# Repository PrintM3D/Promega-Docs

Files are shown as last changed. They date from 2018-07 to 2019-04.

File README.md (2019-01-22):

# Welcome!

Welcome to the  M3D Promega's User Manual.

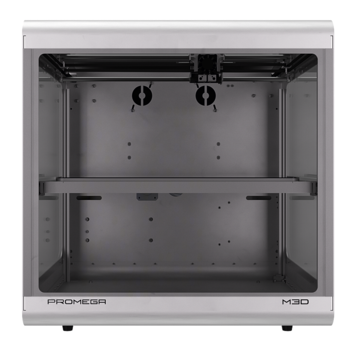
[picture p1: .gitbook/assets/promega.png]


## Features

### Expandable

The Promega is expandable, meaning you can customize it to suit your needs. These are 4 possible extruder configurations.

{% tabs %}
{% tab title="Compound Printing" %}
The Compound nozzle is a dual mixing nozzle, which takes in two filaments and either prints one at a time or mixes them together. 

A standard Promega will come with this extruder.

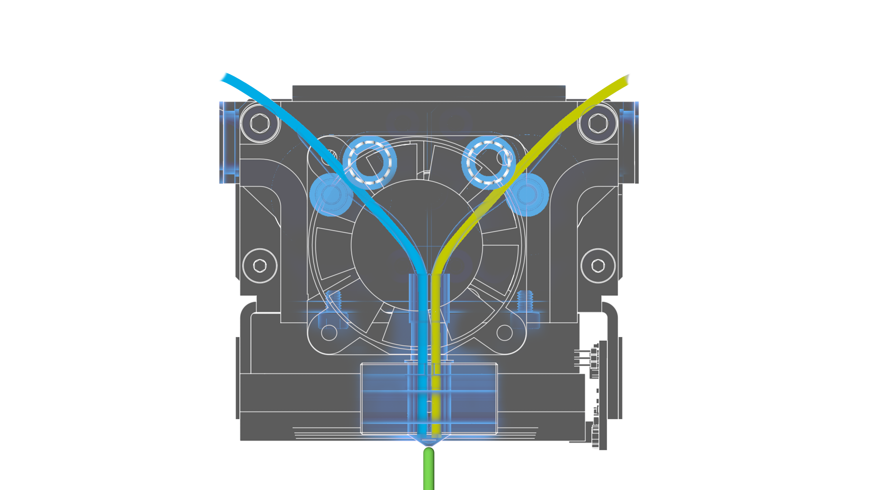
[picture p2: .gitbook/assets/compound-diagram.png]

{% endtab %}

{% tab title="Dual Printing" %}
  
The K'Tana hot end is two, independent nozzles for dual printing. 

K'Tana nozzles are seamless, long nozzles that include a thin-wall heat break to reduce energy consumption and eliminate leaks.

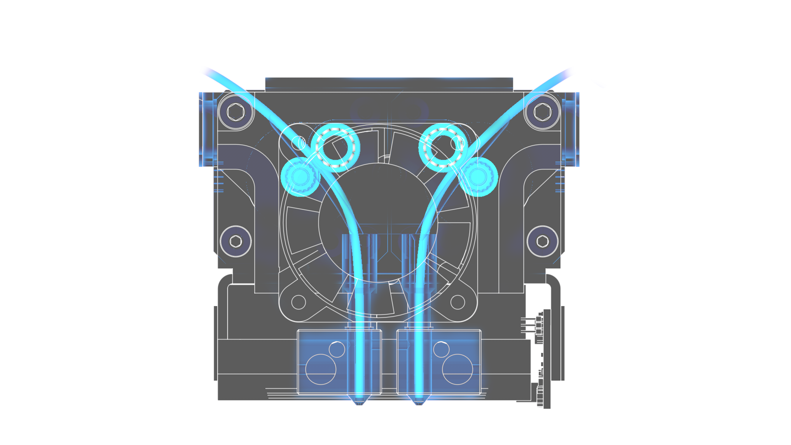
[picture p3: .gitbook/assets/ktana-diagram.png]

{% endtab %}

{% tab title="Quad Printing" %}
  
The Quad extruder takes in four filaments and can either print one at a time or mix for blended colors.

You can create beautiful color prints using our CMYK color-calibrated mixing filament.

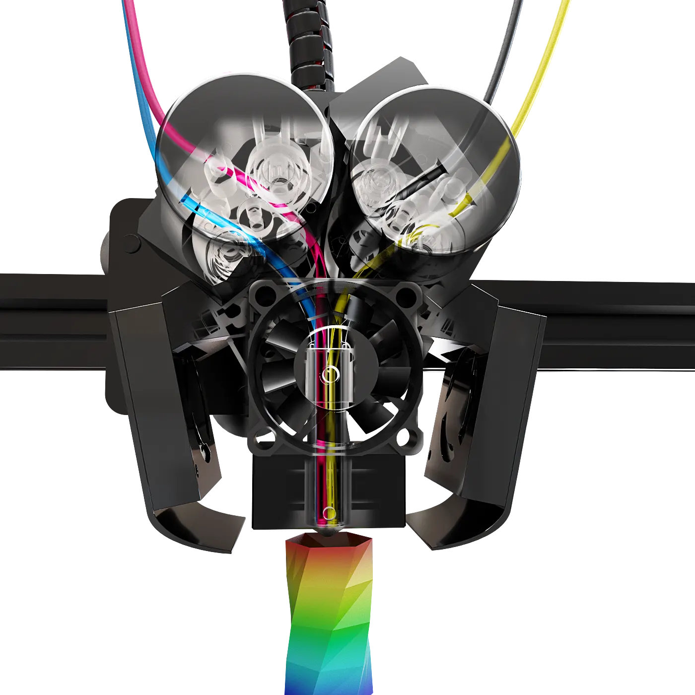
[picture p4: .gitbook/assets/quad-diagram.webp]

{% endtab %}

{% tab title="High Temp Printing" %}
Our high-temp extruder add-on allows you to extrude materials up to 350 C. 

This upgrade is ideal for printing high-temp materials such as PEEK, if you are producing small prints. 

For larger prints, you may need a more robust system upgrade. If you are interested in this, please fill out this [form](https://airtable.com/shrPYVe4EY4mXUM4e).
{% endtab %}
{% endtabs %}

Feel free to browse the [part store](https://store.printm3d.com/collections/parts) for more.

### 20" All Metal Frame

Fully enclosed in a 20" all-metal frame.

### 15.3" Cubic Build Volume

15.3"-cubed build volume makes printing just about anything possible.

### Open Source

Both the [Duet3D electronics](https://www.duet3d.com/) and the [Promega parts](documentation/) are open-sourced.

## Where To Start

Please start with the [Beginner Guides](beginners-setup-guides/).

If the Beginner Guides aren't enough, try our [Advanced Guides](advanced-setup-guides/). 

## **Other Resources**

### Duet3D Board

#### [Firmware/Software](https://github.com/PrintM3D?tab=repositories)

#### [Duet Maestro](https://duet3d.dozuki.com/c/Duet_2_Maestro)

#### [Duet GCodes](https://duet3d.dozuki.com/Wiki/GCode)

### Promega Parts Store

#### [Linked Here!](https://store.printm3d.com/collections/parts/printer-model_m3d-promega)

### Open Source 

#### [Public Google Drive](https://drive.google.com/open?id=1cmnAcQU7NjgBqAub60Pz7tJyY-e5qH1w)

{% hint style="info" %}
Houses all iterations of:

* SD Cards
* Slicer
* Printed Part. 
{% endhint %}

### **Q&A Promega Users**

[Submit Issue](https://github.com/PrintM3D/Promega/issues). Allows you to search for existing issues to upvote them. 

Submit a new issue if you do not find one.

### Contributing

Please feel free to add suggestions to any of the guides by creating a pull-request or issue on [GitHub](https://github.com/PrintM3D/Promega-Docs/issues). This manual is hosted in Github.com via Gitbook.com.

The main way to collaborate to the guides is to become a collaborator. But sometimes you simply want to submit a small contribution, without becoming a regular collaborator.

On GitHub, one can use the popular _Pull Request_ feature. To do so, you would clone [https://github.com/PrintM3D/Promega-Docs](https://github.com/PrintM3D/Promega-Docs), make changes on your own copy, and submit back your changes by submitting a _Pull Request_ to M3D. Then we will review the changes accordingly.

#### Let's Get Started!

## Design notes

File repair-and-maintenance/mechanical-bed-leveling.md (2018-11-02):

# Mechanical Bed Leveling

### Leveling the Bed

As covered in the [Bed Leveling & Probing](../advanced-setup-guides/bed-leveling-and-probing.md) guide, bed leveling compensation will work for differences of about 3mm across the entire bed. Leveling your bed can be done by skipping teeth on the bed in specific corners. If your bed is extremely un-leveled, it will not be movable by hand.

Look at your bed and determine if one side is visibly higher than the other side.

Remove the binder clip if you have placed one on the Z-motor belt.

Gently pull up on the corner that you want to skip. Apply pressure until you feel the corner give with a loud click. 

{% hint style="warning" %}
Do not skip the bed near the belt clamps as it can break your belt clamps.
{% endhint %}

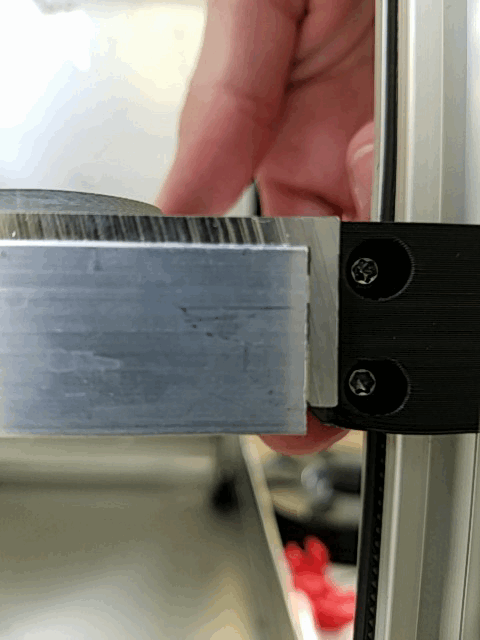
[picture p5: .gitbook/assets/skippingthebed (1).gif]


Once the bed is level enough to the point where it drops by itself, move the bed up to the nozzle by hand. The bed is best lifted up from the points pictured below. 

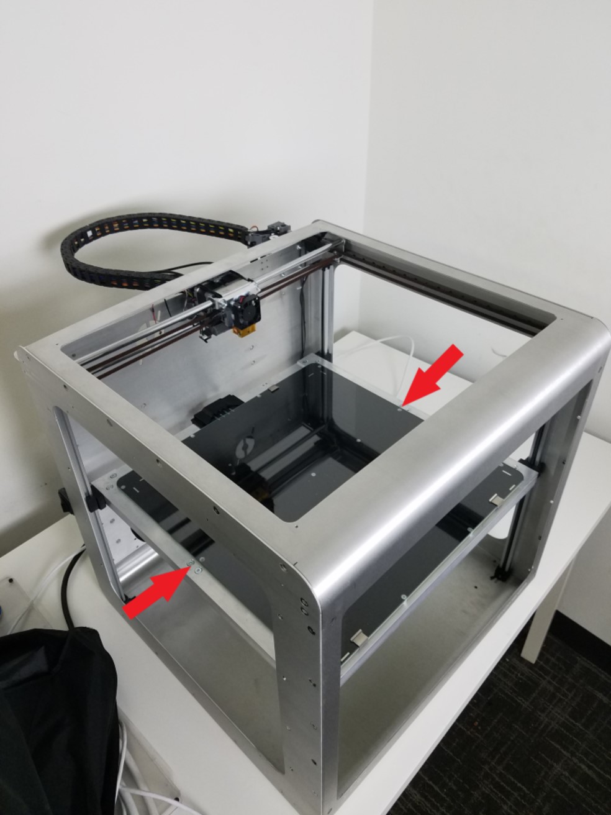
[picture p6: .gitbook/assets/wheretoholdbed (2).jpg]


Lift slowly or you will skip the bed. 

{% hint style="warning" %}
Moving the bed too fast can also fry your Duet board, so be careful.
{% endhint %}

When the bed is touching the nozzle, determine the offset of the Z-sliders to the top belt clamps to determine whether the bed is level. This will give you a good enough estimate to level the bed.

{% hint style="info" %}
Bed leveling compensation with `G29` can take care of the rest.
{% endhint %}

Comparing the Distance in Each Corner

{% hint style="info" %}
The bed can be leveled more accurately by using a caliper to measure the distance between the bed and the top of the Z-slider rails and comparing the corners.
{% endhint %}

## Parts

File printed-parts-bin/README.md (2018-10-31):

# Your Printer's 3D Parts

For all printed part iterations, click [here](https://drive.google.com/drive/u/0/folders/1cmnAcQU7NjgBqAub60Pz7tJyY-e5qH1w).

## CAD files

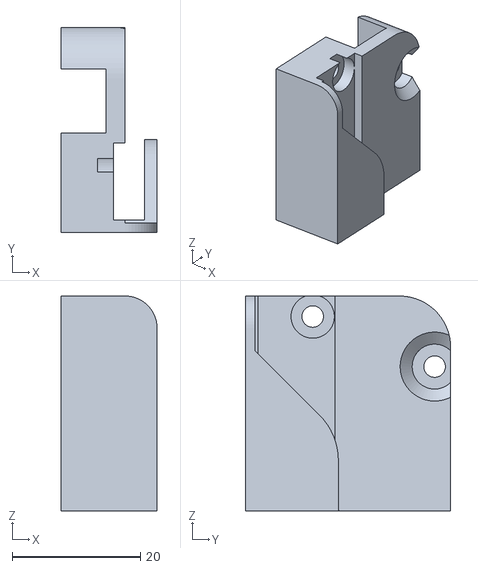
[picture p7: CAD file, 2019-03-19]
.gitbook/assets/y-limit-housing-xl-v2_2.stl
15.0 x 32.0 x 33.5

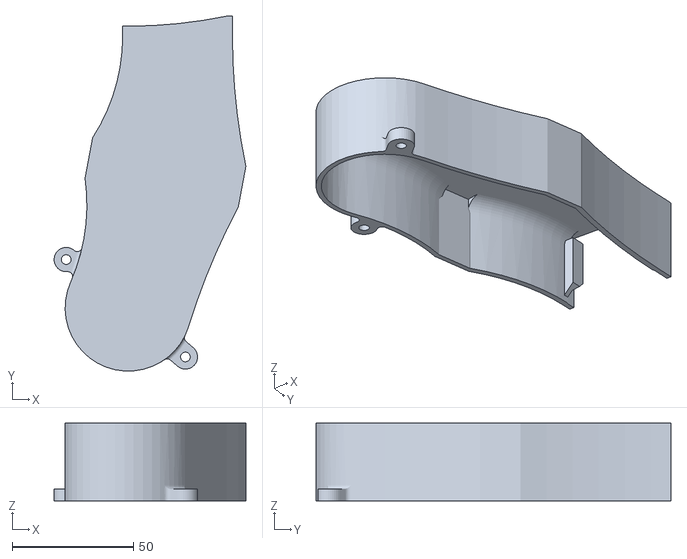
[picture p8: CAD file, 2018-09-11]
.gitbook/assets/a2-external-filter-fan.STL
79.0 x 146.2 x 32.1

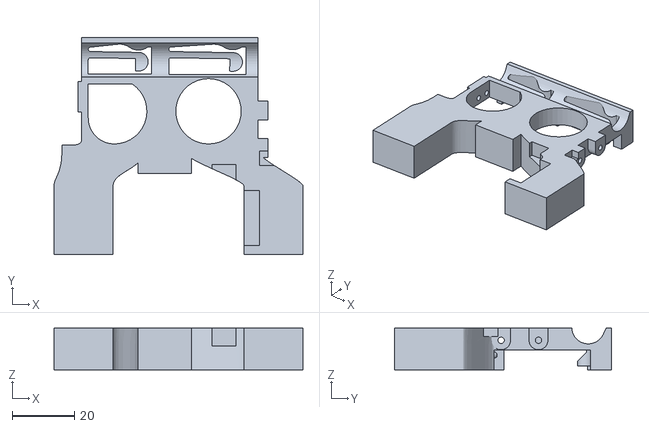
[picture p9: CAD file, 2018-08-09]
.gitbook/assets/nozzle-fan-duct-rv7_6.STL
80.0 x 69.8 x 13.4

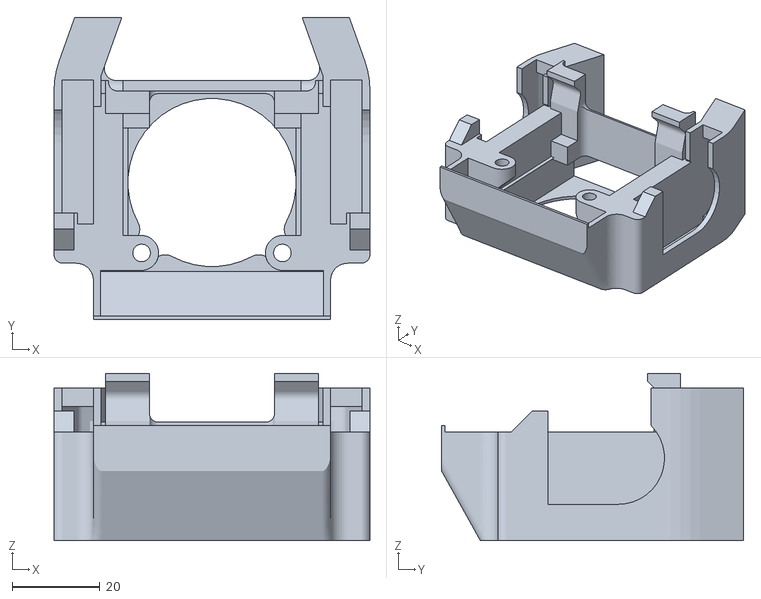
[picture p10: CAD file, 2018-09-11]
.gitbook/assets/058052_a4-nozzle-fan-guide.STL
71.8 x 68.6 x 38.0

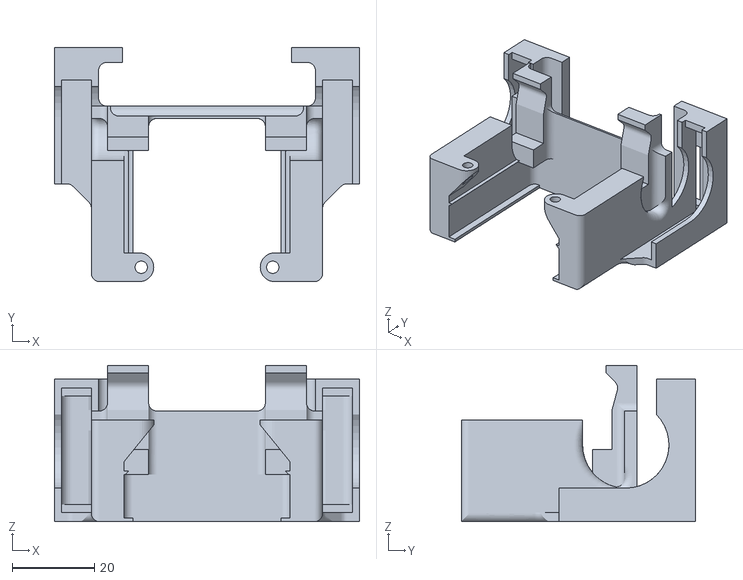
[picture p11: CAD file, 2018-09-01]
.gitbook/assets/058052_a3-nozzle-fan-guide.STL
74.2 x 57.0 x 38.0

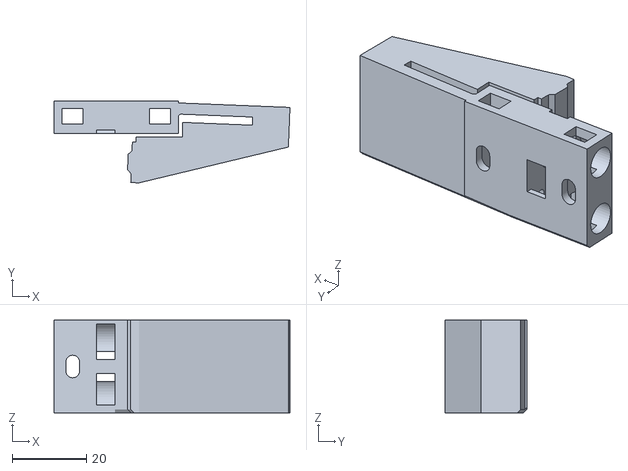
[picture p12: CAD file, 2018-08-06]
.gitbook/assets/051296_b4-z-slider_rv14_1 (1).STL
63.7 x 22.1 x 25.0

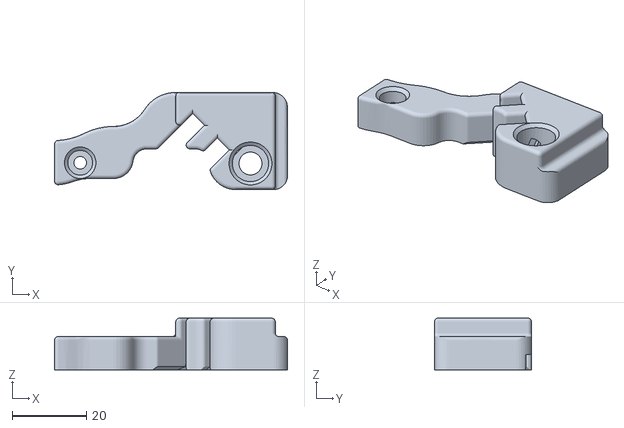
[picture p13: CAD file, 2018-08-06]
.gitbook/assets/051134_a2-rear-cable-harness-support.STL
62.9 x 26.2 x 14.0

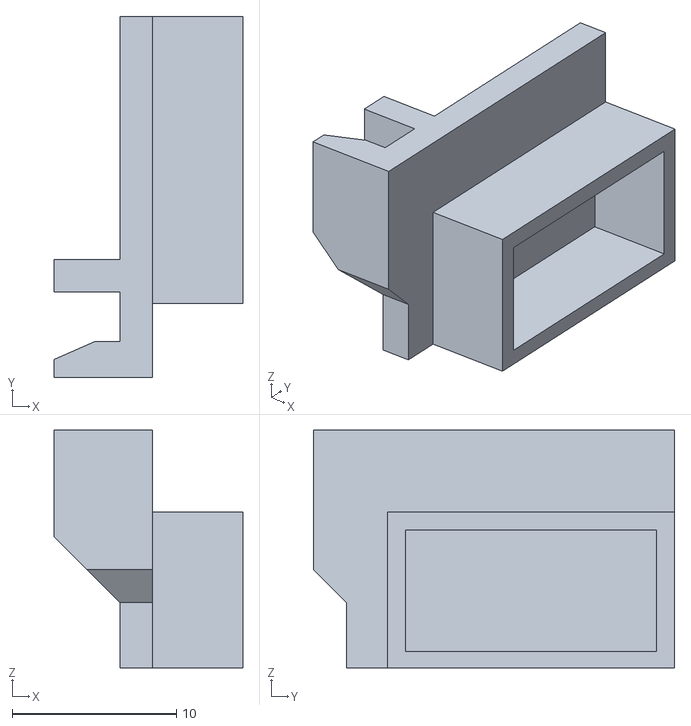
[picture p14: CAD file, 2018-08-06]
.gitbook/assets/051405_a1-magnet-holder-right.STL
11.5 x 22.0 x 14.5

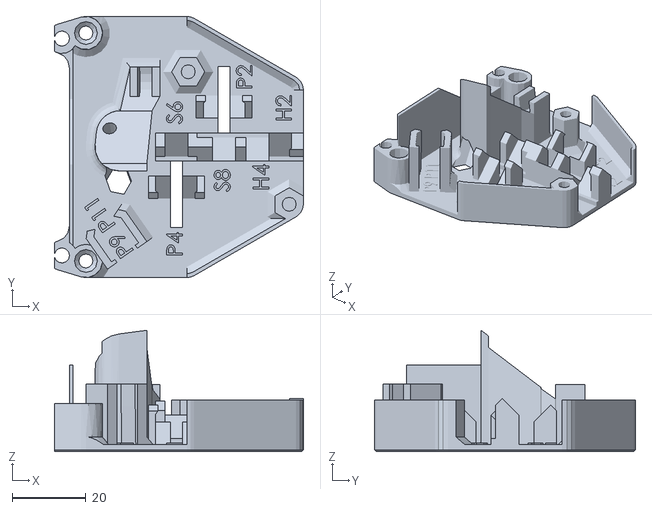
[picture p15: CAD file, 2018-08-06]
.gitbook/assets/058302_b1-front-cable-harness-base.STL
67.4 x 70.7 x 32.9

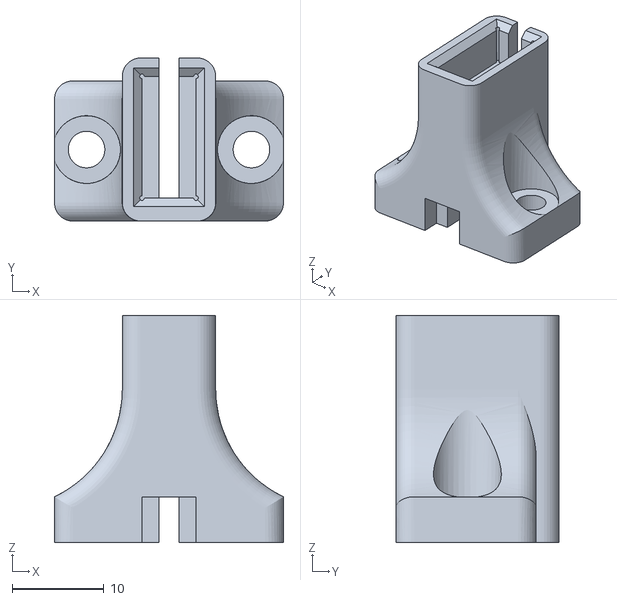
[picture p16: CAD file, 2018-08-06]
.gitbook/assets/051162_b1-z-limit-switch-holder.STL
25.0 x 17.8 x 24.8

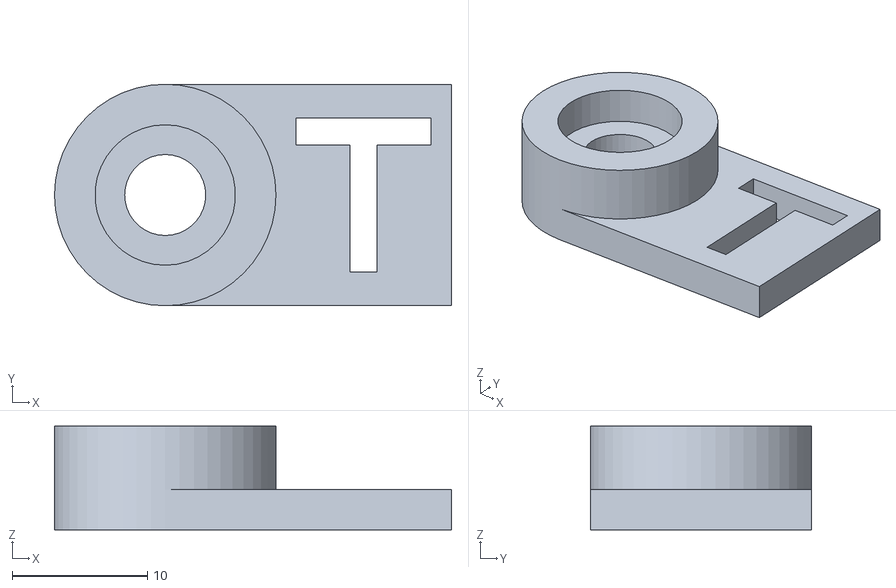
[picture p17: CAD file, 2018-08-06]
.gitbook/assets/051132_a1-bearing-standoff-height-offset.STL
29.4 x 16.4 x 7.70

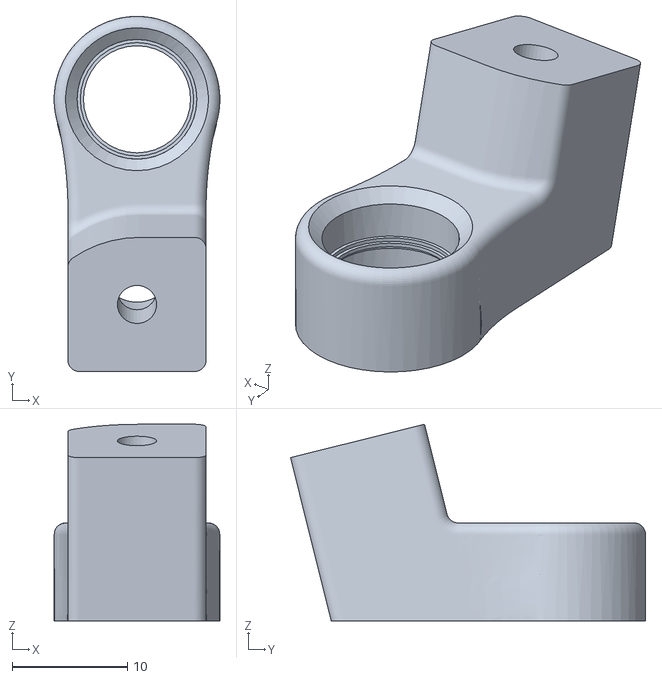
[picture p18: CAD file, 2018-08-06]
.gitbook/assets/051108_c1-rear-cable-harness_base.STL
14.4 x 30.8 x 17.1

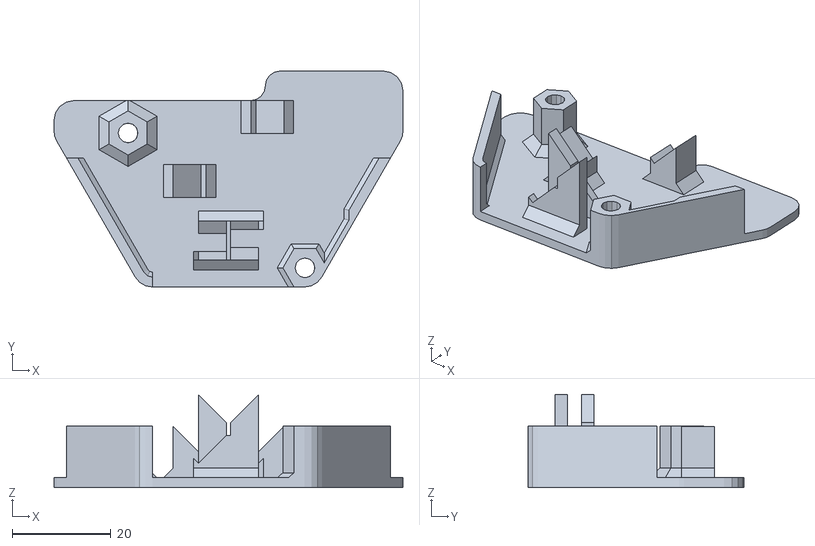
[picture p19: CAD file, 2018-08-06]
.gitbook/assets/058304_a3-front-cable-harness-cover.STL
70.7 x 43.8 x 18.9

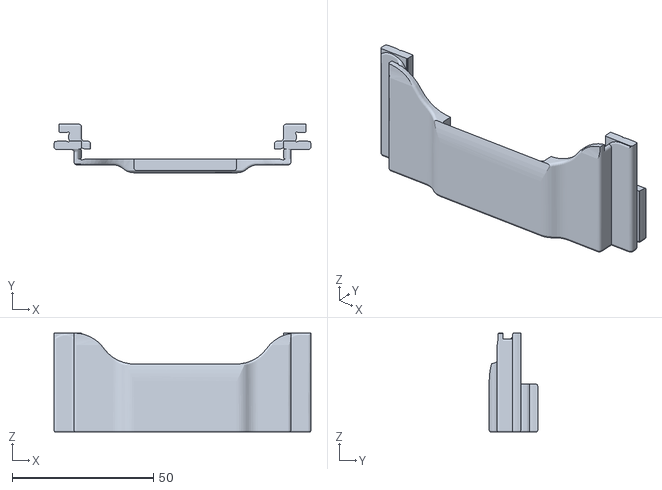
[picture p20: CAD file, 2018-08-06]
.gitbook/assets/051224_a3-bed-terminal-cover.STL
91.0 x 17.2 x 35.0

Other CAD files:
.gitbook/assets/051404_b1-z-bottom-belt-clamp.STL
.gitbook/assets/051108_d1-rear-cable-harness_base.STL
.gitbook/assets/051172_b1-bed-_-power-switch-holder.STL
.gitbook/assets/058304_a2-front-cable-harness-cover.STL
.gitbook/assets/051112_b1-spool-holder.STL
.gitbook/assets/051134_a1-rear-cable-harness-support.STL
.gitbook/assets/051162_b2-z-limit-switch-holder.STL
.gitbook/assets/051166_b1-x-limit-switch-holder.STL
.gitbook/assets/051166_c1-x-limit-switch-holder.STL
.gitbook/assets/051168_b1-y-limit-switch-holder.STL
.gitbook/assets/051168_b2-y-limit-switch-holder.STL
.gitbook/assets/051172_b2-bed-_-power-switch-holder.STL
.gitbook/assets/051174_a1-bed-limit-housing.STL
.gitbook/assets/051174_a2-bed-limit-housing.STL
.gitbook/assets/051176_a1-bed-limit-slider.STL
.gitbook/assets/051176_a2-bed-limit-slider.STL
.gitbook/assets/051224_a1-bed-terminal-cover.STL
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

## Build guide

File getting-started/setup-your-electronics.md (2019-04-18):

# Setup Your Electronics

## Check Your Power Supply's Input Voltage

{% hint style="warning" %}
Failure to do so will DAMAGE the power supply.
{% endhint %}

There are two input wall voltages: 115V or 230V. Choose the appropriate settings.

{% embed url="https://www.worldstandards.eu/electricity/plug-voltage-by-country/" caption="" %}

### How To Switch Between Voltages

The switch, used to flip between 115V and 230V, is located on the bottom part of the power supply.

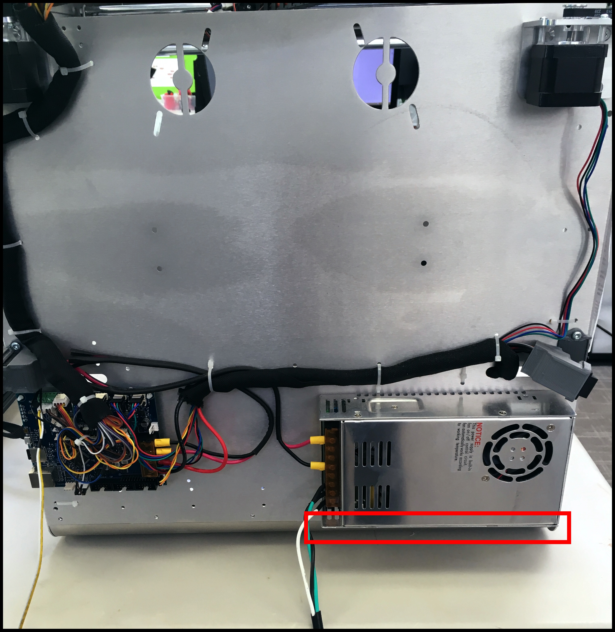
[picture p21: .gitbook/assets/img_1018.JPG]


Use a flat head to manually slide the switch. The current state of the switch is labeled.



## Your SD Card

### Accessing the microSD

Updating any configuration or G-code files without connecting to your printer is possible by changing the required files on the microSD card. The microSD card is located in a microSD port on the ProMega's Duet Maestro board. By pushing the microSD card into the board, as the arrow indicates in the image below, the microSD card will be released from the board. The microSD port and the Duet Maestro are sensitive, so be careful when removing microSD cards.

Location of the microSD Port on the Duet Board

You can plug the microSD card into the microSD card reader included with your Promega. The microSD card reader can then be plugged into your computer's USB port. The microSD card should then appear as a drive to your computer. You will now be able to download and change any of the files on this card.

SD Card Structure

### Introduction Video

On the microSD card you will find numerous introductory files and a video. Review these materials!

{% hint style="info" %}
Videos only apply to Promega Compounds & K'Tanas \(not Promega Quads\).
{% endhint %}

Whenever you are done changing files on the microSD card it is best to safely eject the card and insert it back into the board. It is best to remove and insert the microSD card when the board is powered off. Continue to the Network setup guide with the button below.

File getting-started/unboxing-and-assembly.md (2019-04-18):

# Unboxing & Assembly

## Before Opening

Check the outside of the packaging for any significant amount of damage that might have occurred in shipping. We recommend taking pictures of the box in case the Promega was damaged in shipping. In this box you will find various small items in different packages. Please thoroughly check all wrapping and padding before discarding them to ensure you keep all parts. Keep the Promega's box intact in case you need to transport the printer in the future.

**Warning: The Promega's frame can be sharp. Please take care when moving the printer in this procedure.**

## Opening the Box

1. Cut through the tape of the box on the top. Do not cut deep as the Promega is located below! 
2. Remove the top and side cardboard layers and bubble wrap.
3. Carefully lift the Promega from the box. Lift from the points indicated in the image below. **Do not lift from the frame member at the back \(marked by red cross\).**

   

4. Remove any additional padding from the box to ensure no other parts remain in the box.
5. Remove plastic wrap from the printer. You should now see items on the bed of the printer. The package includes important items, please take care when opening.

   

6. Remove the tape from the coreXY assembly.

   

7. Remove the tape holding the items and the Z-platform down.
8. Remove the items from the bed of the printer. 
9. Lift the Z-platform as shown in the image below and remove foam blocks from under the bed.

   

## Items Included

1. microSD Card + microSD Card Reader
2. Spool Holders

   

3. Windows \(Optional: Glass Bed\)

   

4. Rubber Feet x4

   

5. microUSB Cable

   

6. Optional: Glass Bed Clamps x4

   

### Mounting the Spool Holders

The spoolholders should be placed on the back of the printer. Two M4 T20 Torx Countersunk bolts and a locknut hold the spoolholder in place.

 

## Mounting the Feet

Follow this section to attach the feet to the printer. You will need a T20 Torx screwdriver.

1. The base of the printer has four holes intended for the feet of the Promega.
2. Carefully flip the printer on it's front in order to get access to the bottom of the printer.

   

3. Take the M4 bolts out of the bag and screw them into the feet with a T20 Torx tool.  
4. You can now attach the feet to the base of the Promega through the holes in the picture in step 1. Tighten the feet down with the included M4 lock-nuts.

## Attaching the Glass Bed

Attaching the glass bed clamps to the glass bed can be tricky. Using a flathead screwdriver as a wedge makes it a lot easier!

1. Use the flathead screwdriver to open the clamp as shown. Try different sized flathead screwdrivers if this is too difficult. If the clamp is too tight to mount on the bed you can rotate the flathead screwdriver in the clamp to open it up more.

   

2. Use the flathead screwdriver to open the clamp and slide one side on the bed as shown.

   

3. Once you have one side on, remove the flathead screwdriver and simply slide on the clamp

   

## Attaching the Switches

To prevent damage while shipping, the power switch and heated bed coil switch are not connected. You can attach these in the following section.

You will need two M4 12mm Bolts and two M4 nuts per side. You will also need a T20 Torx screw-driver and an M4 wrench or pliers. Screw on both the power switch and the heated bed coil switch.

{% hint style="info" %}
Due to a mistake, M5 nuts were shipped with a few Promegas instead of M4 nuts.
{% endhint %}





## Installing Windows

This section will walk you through installing your top, side and front windows on your Promega. **This step is optional and can be performed at a later time when you prefer to print with a full enclosure.** All screws needed for this section should be included in the plastic bag.

### Front Window

The front window has four small screw heads that lock onto small magnets located on the front of the Promega. The front window can be identified by the 4 small black screws sticking out of it. Face the screws toward the frame and simply stick it on the Promega.





### Top Window

Next, we will install the top windows. You can find the top window by finding a thicker piece of plastic that does not have screws in it. For this you will need 4 12mm M3 bolts and a T10 Torx screw-driver. Screw in the M3 bolt on all four sides as shown in the image below.







### Side Windows

The side windows can be identified by the fact that they are made of thinner plastic, and that there are two of them. For the side windows you will need 8 \(4 for each side\) M3 5mm bolts. You can screw these into place with the T10 Torx Screw Driver as shown in one of the images below. The side windows go on the inside of the Promega.

Four M3 5mm Bolts



Continue on to [Mechanical Check](check-your-printer.md), the next chapter in the [Getting Started](./) guide.

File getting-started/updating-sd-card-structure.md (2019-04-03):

---
description: Update the contents of the Duet Maestro microSD card.
---

# Updating SD Card Structure

While your printer was being shipped, it is possible that a new SD card structure was released. More explanation of the SD Card files can be found in the next guide. To ensure that you have the latest files on your SD card, please follow the guide below.

## M3D Release SD Card

The latest SD card files released by M3D can be found on the [M3D Github ProMega Repository](https://github.com/PrintM3D/Promega). Follow the steps below in order to download the latest version for your printer. Always be careful when downloading the latest version of the SD card files. New SD card files can cause unintended results such as flipped motor directions or wrongly configured heaters. **Always test all motors and heaters carefully before printing after downloading a new update.**

Read the [Accessing Your SD Card](setup-your-electronics.md#accessing-the-microsd) for more help on getting to the SD card files.

Read the [SD Card Structure](../documentation/software-firmware/sd-card-structure.md) guide for more explanation on the files and directories on the SD card.

{% tabs %}
{% tab title="Downloading Directly from the Repository" %}
## Downloading Directly from Repository

This option is not always recommended, but it will allow you to get the latest configuration files, regardless of official release. Once you have found and opened the [M3D Github ProMega Repository](https://github.com/PrintM3D/Promega). Press the _Clone or download_ button circled below and then click _Download ZIP_. This will download a _.zip_ file of the repository.

Downloading from Github
{% endtab %}

{% tab title="Downloading Official Release" %}
## Downloading Official Release

This is the recommended option.

Go to the [M3D GitHub Promega Repository Releases](https://github.com/PrintM3D/Promega/releases) and download the latest release. Download the _.zip_ folder for the extruder head that you currently have mounted. The Promega can come with either the K'tana \(two nozzles\) or the compound \(1 nozzle\).

Downloading the Latest Release
{% endtab %}

{% tab title="Downloading Pre-Release" %}
## Downloading Pre-Release

Go to the [Public M3D Google Drive](https://drive.google.com/drive/u/0/mobile/folders/1cmnAcQU7NjgBqAub60Pz7tJyY-e5qH1w?usp=sharing).

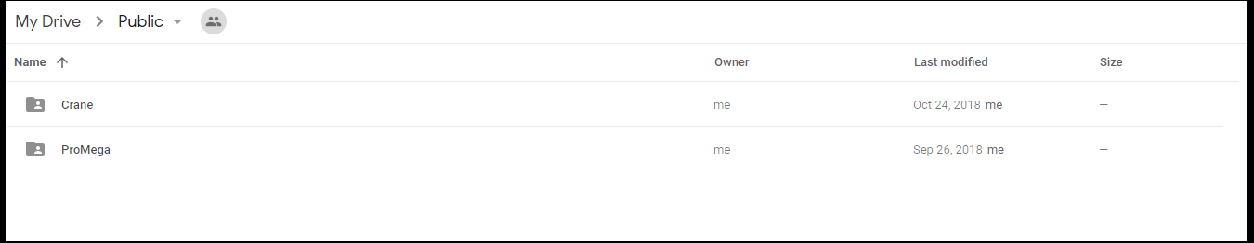
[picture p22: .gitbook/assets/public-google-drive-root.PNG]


Click _**ProMega**_.

Click _**Public SD Release**_.

Browse through the releases. Choose one.

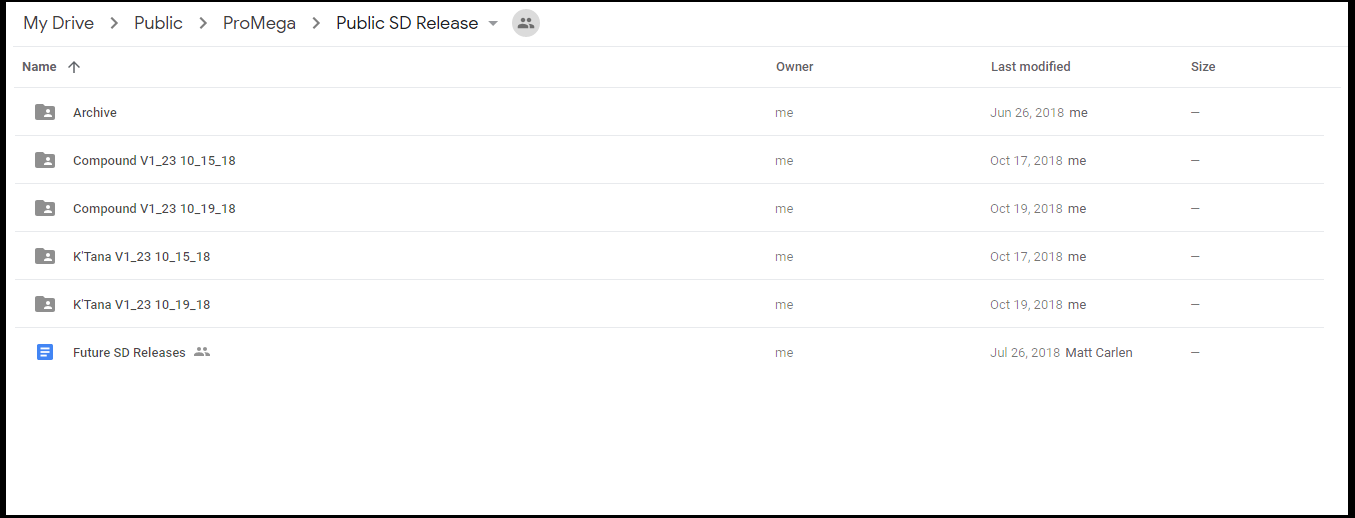
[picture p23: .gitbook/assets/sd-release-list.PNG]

{% endtab %}
{% endtabs %}

## Extracting the Folder

A _.zip_ file is a compressed folder. You will have to first extract the file before you can get to it's contents. Find the file you just downloaded and extract it into a folder. Right click the file and then select _Extract All_. This will move all the files in the compressed file into a folder. You can now access the new SD card files.



## Moving the Files onto the SD Card

**Back-up your SD card files before updating so you can always revert to your original settings**. Now that you have access to the files, locate the _SD Card Structure_ folder in the folder you just extracted. This folder will have two folders _Compound_ and _K'Tana_, select the folder based on what nozzle you currently have mounted on your printer. In both of these folders are the files you want to copy to your microSD card. This should be four folders: _sys, gcodes, macros_ and _www_. Plug in the microSD card into your computer with the microSD card reader and copy the files onto it. Your SD card should look like this. Using WinDiff or a similar program to distinguish differences between the latest SD card release and your files might be a good idea.



## Testing and Tuning

Once you have updated the SD Card files on the microSD card. Test all your motors and heaters one by one to ensure the new settings are compatible with your wiring and board. If you changed any settings in your previous configuration, you will have to add these settings and commands in your new updated version. If any of the motors or heaters are flipped, [this guide](../how-to-troubleshoot/common-troubleshooting/help-my-extruders-are-backwards.md) will help.

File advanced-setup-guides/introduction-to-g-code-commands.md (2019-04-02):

# Introduction To G-Code Commands

Now that you are familiar with the coordinate system of the Promega, its orientation and direction, we can get started with learning and sending G-code commands. G-code commands are sent one line at a time, with one command per line. When you send a print file to your printer in order to print something, you are sending the printer a long list of G-code commands. It will look something like this \(but way longer!\):

```text
G1 X173.448 Y182.05 E0.03872
G1 X173.922 Y181.843 E0.03871
G1 X174.422 Y181.712 E0.03868
G1 X174.883 Y181.662 E0.0347
G1 X178.301 Y181.524 E0.256
G1 X183.787 Y181.051 E0.41207
G1 X189.186 Y180.278 E0.40816
G1 X194.553 Y179.196 E0.40972
G1 X197.18 Y178.55 E0.20245
G1 X202.457 Y177.012 E0.41134
G1 X208.239 Y174.993 E0.45832
G1 X208.864 Y174.84 E0.04815
G1 X209.841 Y174.699 E0.07387
G1 X210.32 Y174.665 E0.03594
G1 X240.74 Y174.665 E2.27649
G1 X241.414 Y174.733 E0.0507
G1 X242.865 Y175.031 E0.11085
G1 X243.362 Y175.174 E0.0387
G1 X243.641 Y175.293 E0.0227
G1 X244.676 Y175.79 E0.08592
G1 X245.287 Y176.169 E0.05381
G1 X245.992 Y176.719 E0.06691
G1 X246.435 Y177.134 E0.04543
G1 X247.028 Y177.801 E0.06679
G1 X247.379 Y178.274 E0.04408
G1 X247.842 Y179.028 E0.06621
G1 X248.113 Y179.576 E0.04575
G1 X248.46 Y180.476 E0.07218
G1 X248.633 Y181.098 E0.04831
G1 X248.792 Y181.998 E0.06839
G1 X248.843 Y182.581 E0.0438
```

#### **Basic Commands**

The command, `G1`, you are see above is called the move command. This is arguably the most important G-code as it allows you to move the printer. Each G-code command consists of a letter followed by a number. `G31`, `M564` and `T0` are all valid G-code commands as well. The Duet Maestro control board runs [RepRap Firmware](https://reprap.org/wiki/RepRap_Firmware). This firmware determines what commands are valid, and which commands are not. You can find all the valid commands that you can send in a long list on the [RepRap Wiki G-codes Page](https://reprap.org/wiki/G-code). After the initial letter-number combination of the G-code command a parameter can follow. This is also visible with the G-code commands listed above, the command `G1 X248.843 Y182.581 E0.0438` has `X248.843 Y182.581 E0.0438` as parameters. Many different G-code commands have optional parameters that can be entered after the initial command.

#### **Absolute vs. Relative in Commands**

With the `G1` command you can move the printer. However, where the `G1` command moves your printer depends on whether you are in absolute or relative mode. Absolute mode is enabled whenever you send the command `G90`, relative mode is enabled when you send the command `G91`. Whenever you are printing absolute mode is typically enabled. If you restart your printer, absolute mode will also be enabled. If you send the command `G1 X150 Y120 Z100` in absolute mode \(`G90`\), the printer will move to the position X = 150mm, Y = 120mm and Z = 100mm, **relative to the origin**. If you send the same command in relative mode \(`G91`\), it will send the printer 150 mm in the positive X-direction, 120 mm in the positive Y-direction and 100 mm in the Z-direction relative to where the printer currently is positioned. The same command can send the printer to two completely different places depending on what mode you are in. As you saw in one of the commands above, the move command, `G1`, can also have an `E` parameter, this allows for a movement of the extruder motor.

#### **Feedrate**

Aside from the `X`, `Y`, `Z` and `E` parameters which allow the printer to move each of the motors, there is one other important parameter `F`. `F` is the feedrate of the motor, or is simple terms, the speed that the motor will travel at. The units of the `X`, `Y`, `Z` and `E` parameters is mm. However for `F` or feedrate the units are `mm/min`. A normal travel feedrate \(speed\) would be 3000mm/min, but for printing the feedrates are typically much lower.

#### **The Movement Buttons**

In one of the steps above you used the buttons in _Machine Control_ to move the printer. What is really happening here is that when you press a button a list of G-code commands are sent to the printer. For example, if you press the X+10 button to move the printer 10mm in the positive X-direction this is what is actually sent:

```text
M120
G91
G1 X10 F6000
M121
```

You might be familiar with two of the G-code commands here `G91` and `G1`. `G91` enables relative mode, so the next move command that is sent will be with respect to the printers current position and not the origin. After the `G91` command, the move command `G1` is sent. This sends the printer 10mm in the positive X-direction at a feedrate of 6000mm/min. The `M120` and `M121` commands are stack push and pop. If you are not familiar with these two programming terms, then don't worry, they are not important to know for a beginning user. All you have to know is that it will disable relative mode `G91` and return to absolute mode `G90`. This is because you want the printer to be back in absolute mode after pressing the move buttons.

#### **Sending G-code Commands**

Now that you are more familiar with G-code commands you can try to complete the steps below in order to see how the printer responds to you sending G-code commands directly to the printer itself.

Find the _G-code Console_ tab in the Duet Web Console.

G-Code Console in the Duet Web Console

This tab allows you to send commands to the printer using the textfield as seen above. Once you enter a command in the text field you can press _Enter_ or press the dark-blue send button. The printer will then process the command and execute it. If the command executed successfully you will see a print out of the command you send in the _Printer Printout_ terminal with a green background. If the firmware encountered an error while trying to process the command, it will printout the command with a red background and more information about the error. 3. This step assumes you have the printer homed from the previous steps. If you have not yet homed your printer, click the _Home All_ button in the _Machine Control_ tab. Try sending the command `G1 X200 Y200`. This will move the printer to 200 mm X and 200 mm Y. Send the command `G1 Z150`. This will move the bed to about 150 mm from the nozzle. 4. You can keep sending commands to move the printer around the build space. The table below represents the limits of the printer, the firmware should prevent you from going past these limits. Still, try to keep your move commands within the build space of the printer. You can also try to change the feedrate of the printer to see how the speed of the printer changes as the printer moves around.

|  | Axes Limits |  |
| :--- | :--- | :--- |
|  | Max \(mm\) | Min \(mm\) |
| X - Axis | 388 | 0 |
| Y - Axis | 388 | 0 |
| Z - Axis | 377 | 0 |

#### **Other G-code Commands**

Of course there are many more RepRap supported G-code commands \(as you might have seen on the [RepRap Wiki](https://reprap.org/wiki/G-code)\). You will come across some of them as you follow this guide. Whenever you have questions about what a command does, you can look up the command in the wiki.

Throughout the different guides you will find G-code in `this format`. That typically means you can execute the G-code command. Comments are denoted by any text following a semi-colon ";". A new line will end the comment.

`G1 X100 ; This is a comment!`

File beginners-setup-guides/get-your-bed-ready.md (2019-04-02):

# Get Your Bed Ready

## Setup Your Bed

### Setup 1: Print Bed Sheet

Clean the bare surface \(no oil or dust\)

Remove some of the adhesive cover from the Bed Sheet.

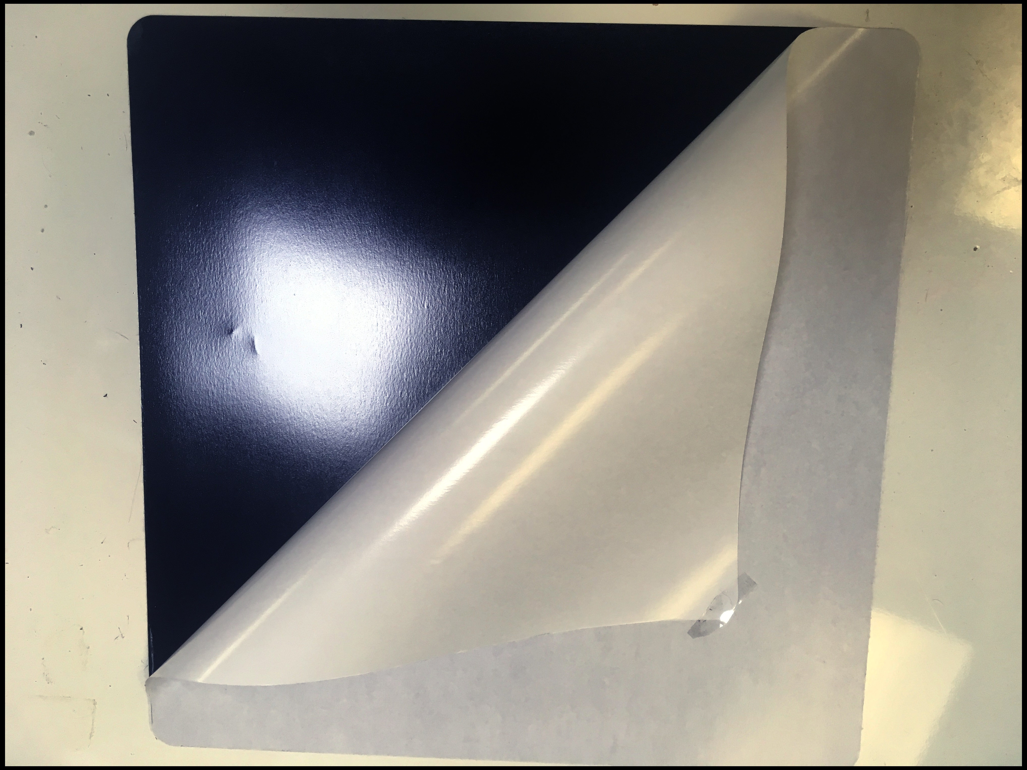
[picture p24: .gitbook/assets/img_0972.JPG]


Pick the front left corner.

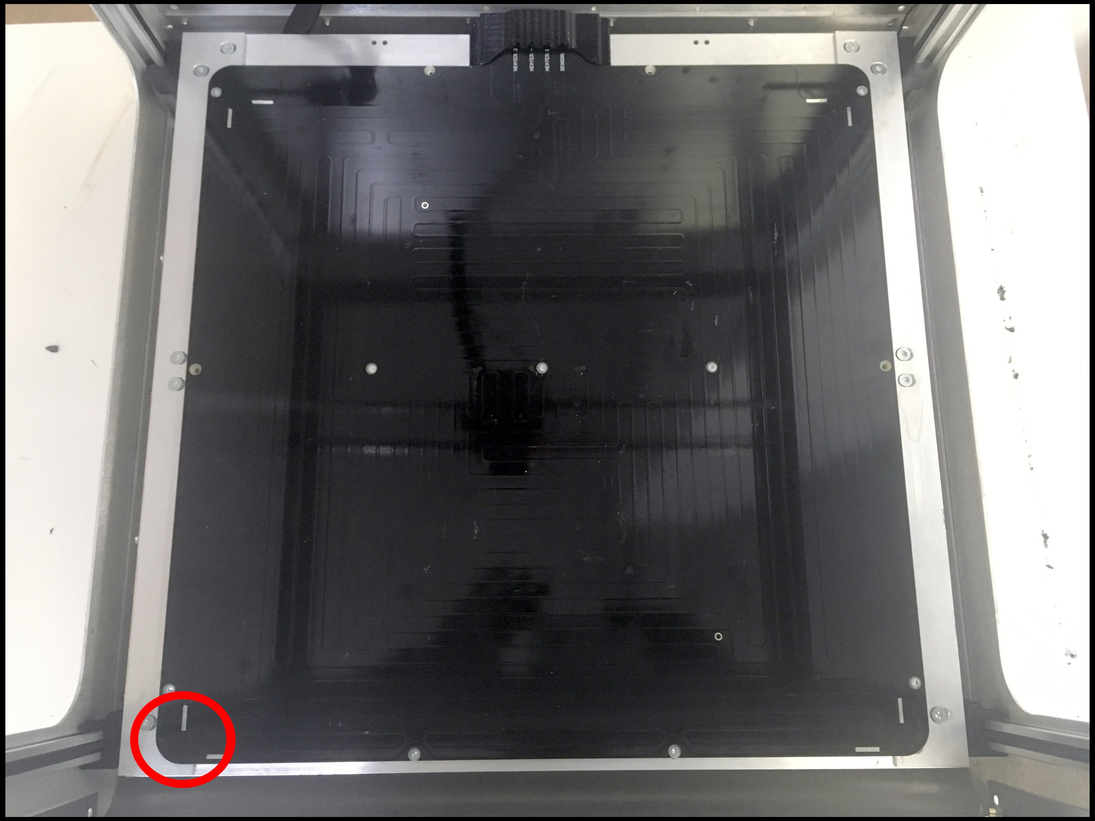
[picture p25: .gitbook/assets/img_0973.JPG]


Stick the corner of the Bed Sheet to the bed.

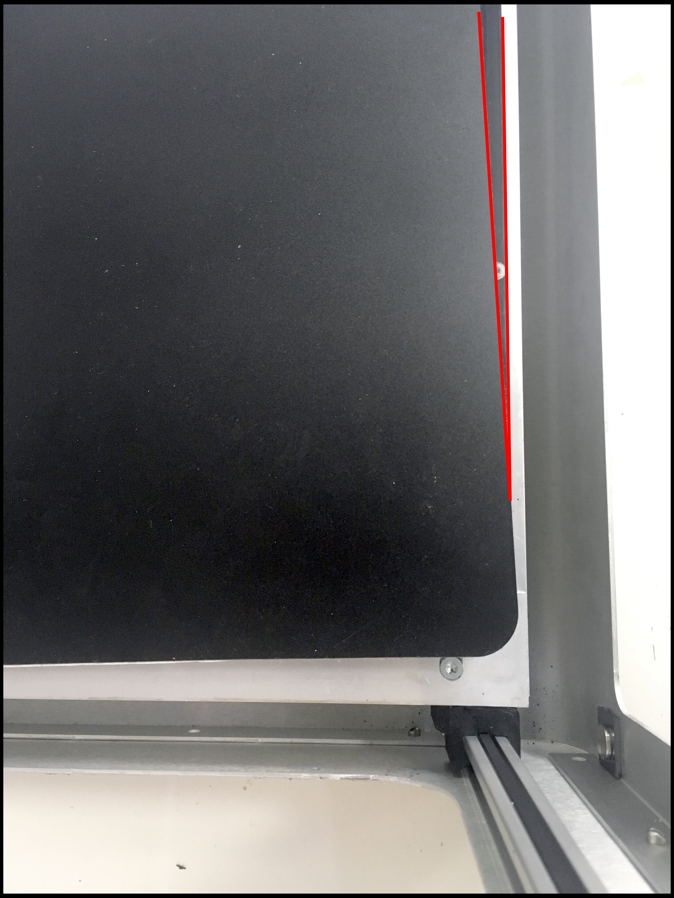
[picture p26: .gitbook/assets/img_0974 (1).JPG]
NOT ALIGNED


Line up the edges.

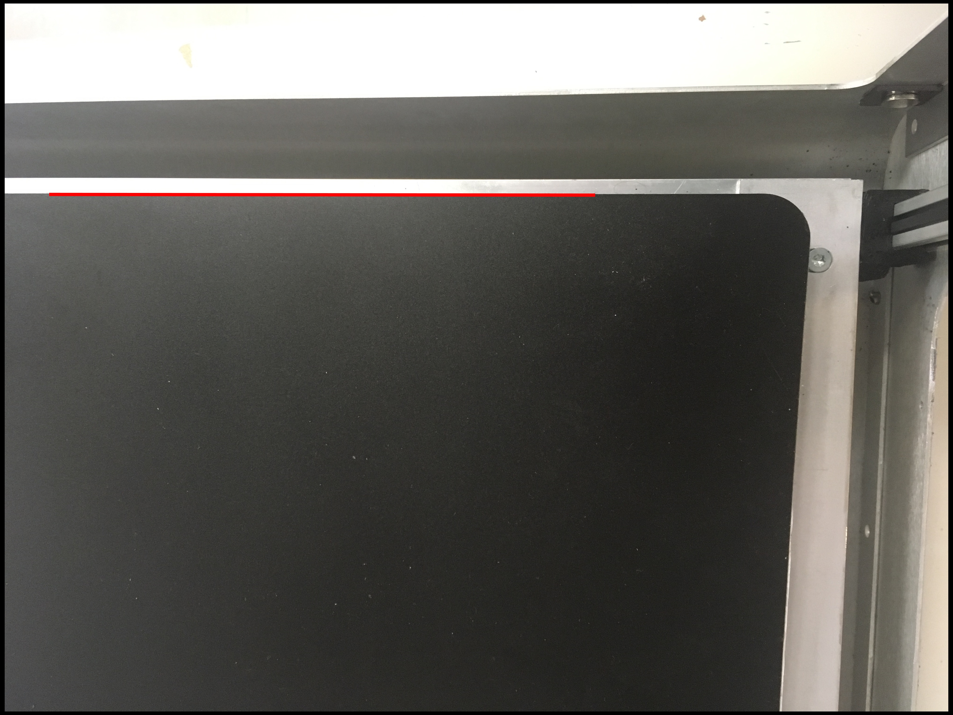
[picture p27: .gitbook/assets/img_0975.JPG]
ALIGNED


Slowly press the Bed Sheet corner into bed.

Check the edges line up \(again\).

Continue pressing down the rest of the Bed Sheet in a WIPING motion.

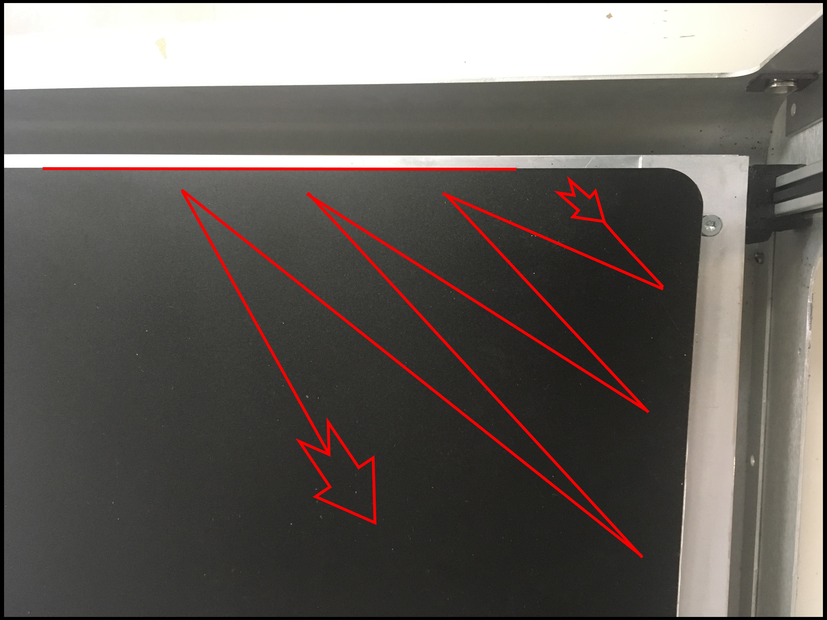
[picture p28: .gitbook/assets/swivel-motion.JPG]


Check the edges line up \(again\).

Remove the rest of the adhesive cover.

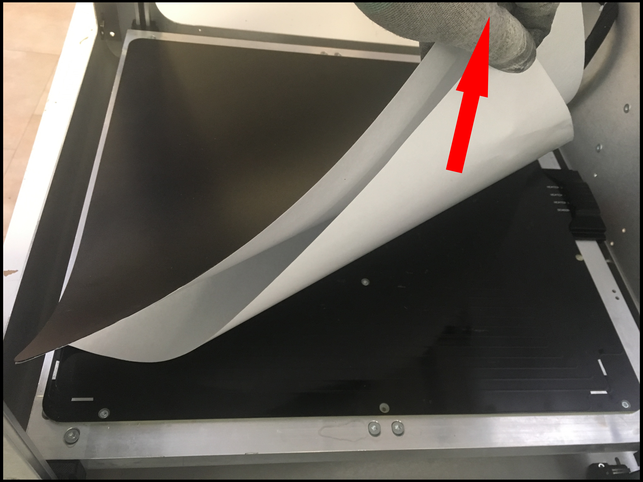
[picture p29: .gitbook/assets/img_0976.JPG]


Finish sticking the rest of the Bed Sheet in a WIPING motion.

### Setup 2: Glass Bed

Pick a position.

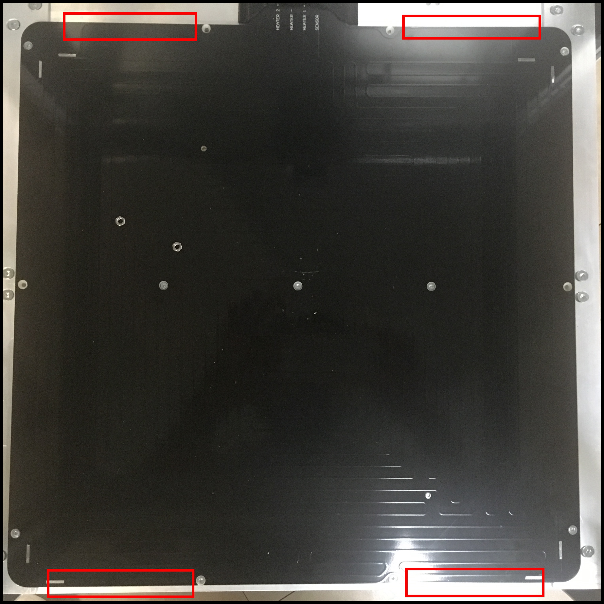
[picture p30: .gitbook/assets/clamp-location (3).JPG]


Get Glass Bed Clamp

Open Glass Bed Clamp with a flathead screwdriver

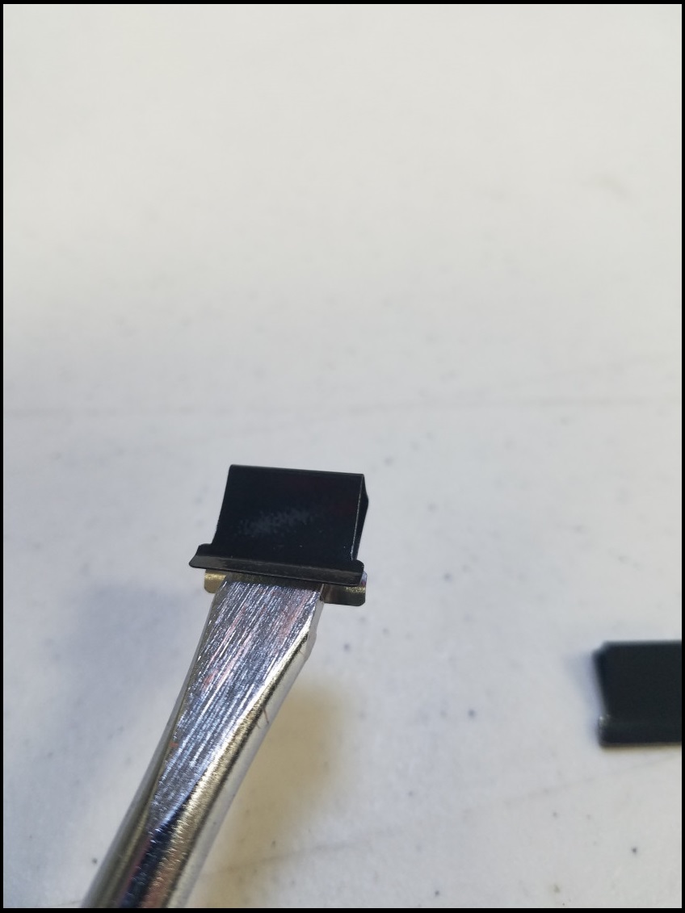
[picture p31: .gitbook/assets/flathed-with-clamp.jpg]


Lay & Align glass bed onto the bed.

Clamp bed.

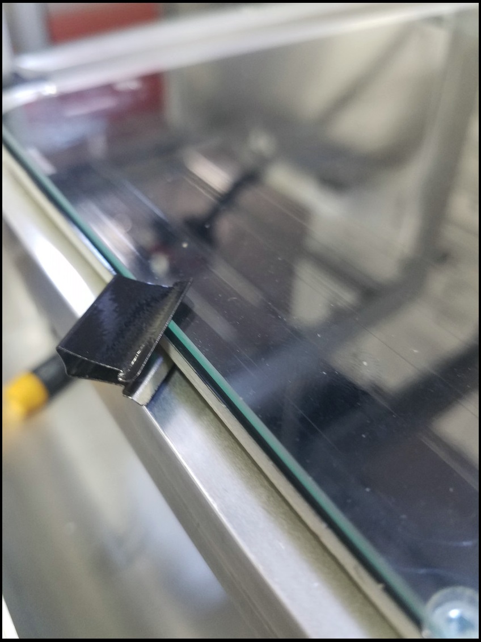
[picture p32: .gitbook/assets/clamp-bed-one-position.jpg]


Slide clamp all the way in.

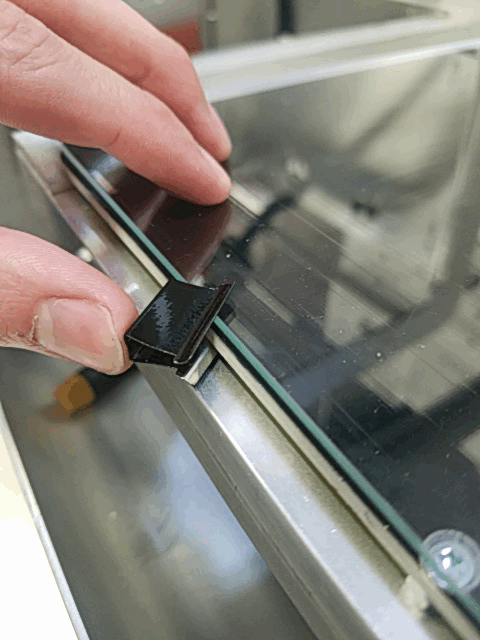
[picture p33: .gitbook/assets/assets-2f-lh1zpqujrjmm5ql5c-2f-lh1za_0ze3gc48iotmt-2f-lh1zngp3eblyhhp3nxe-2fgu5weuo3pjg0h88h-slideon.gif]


Repeat until all positions are clamped.

## Setup Bed Probe

### Press Home All Button

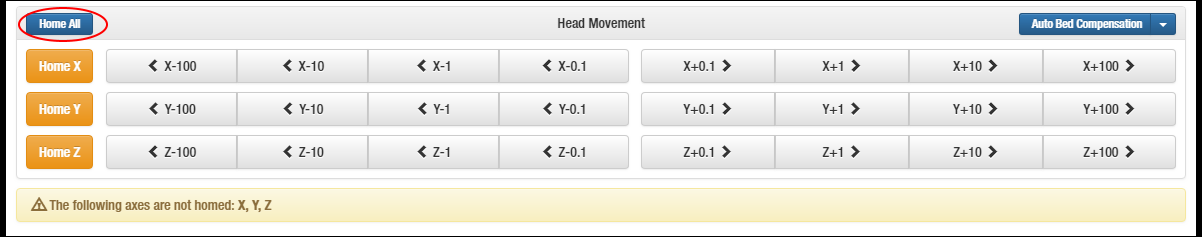
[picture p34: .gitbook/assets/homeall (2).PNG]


### Send the extruder toward center

```text
G1 X187 Y154
```

#### Minor G-code Lesson

G1 = Linear Movement

X\#\#\# = X position

Y\#\#\# = Y position

Z\#\#\# =  Z position

### Heat The Bed

```text
M140 S60
```

#### Minor G-code Lesson

M140 = Set Bed Temperature

S\#\#\# = Bed Temperature \( Celsius\)

### Code Inputs

```text
G31 P999 X-40 y28.5 Z0
G29 S2
M564 S0
```

Wait for bed to reach its temperature.

#### Engage Bed Probe

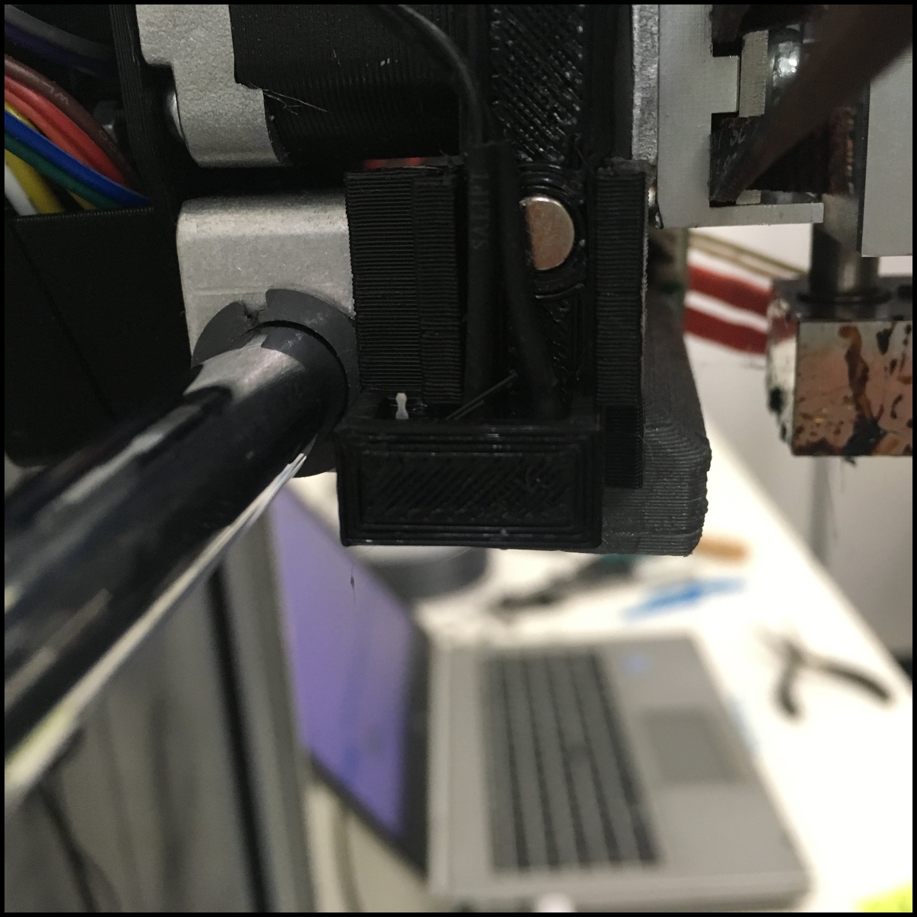
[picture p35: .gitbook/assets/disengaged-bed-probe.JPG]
DISENGAGED


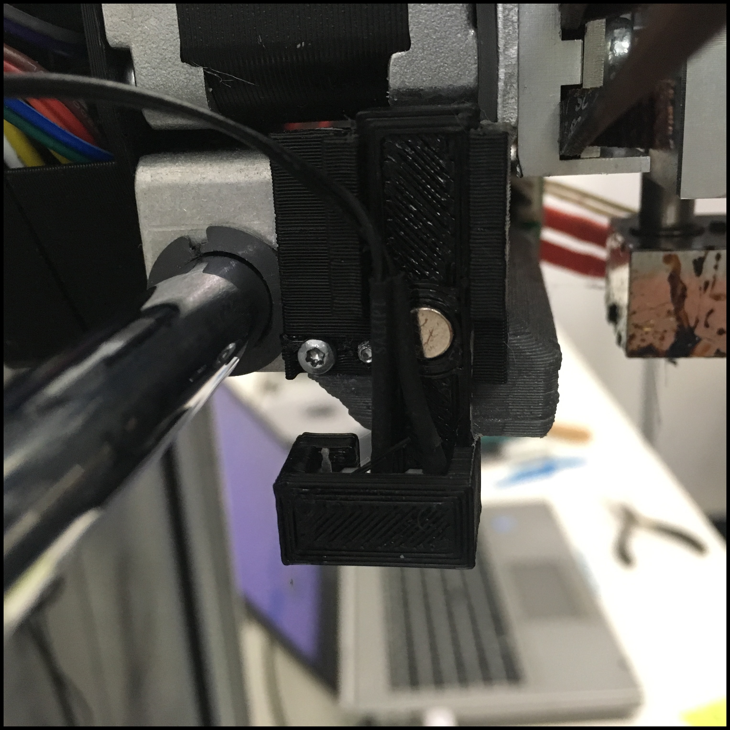
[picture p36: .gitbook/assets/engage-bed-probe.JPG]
ENGAGED


#### Move Bed To Position

```text
G1 Z15
```

### Probe

```text
G30
```

### 

#### Disengage Bed Probe

#### Move Bed Closer

```text
G1 Z0
```

### Move Bed To Nozzle

Use these two buttons to move the bed up.

Ignore the yellow home blocks \(for now\).

Switch to the smaller 0.1 mm step when you get close to the nozzle

### Record Z offset

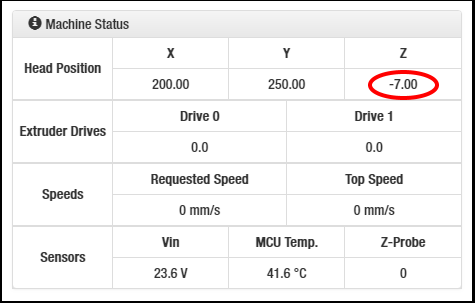
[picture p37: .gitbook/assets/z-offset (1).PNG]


### More Code Inputs

Replace \#\#\# with the Z offset number from the last step.

The number is POSITIVE ONLY.

```text
G31 P999 X-40 Y28.5 Z###
M564 S1
```

#### Move Bed To Position

```text
G1 Z15
```

### 

#### Engage Bed Probe \(Again\)

### Probe \(Again\)

```text
G30
```

### 

### Disengage Bed Probe \(Again\)

### 

### Check nozzle height

```text
G1 Z0
```

The bed should be about a paper sheet away from the nozzle.

### Save Into SD card.

Go to the System Editor tab under Settings

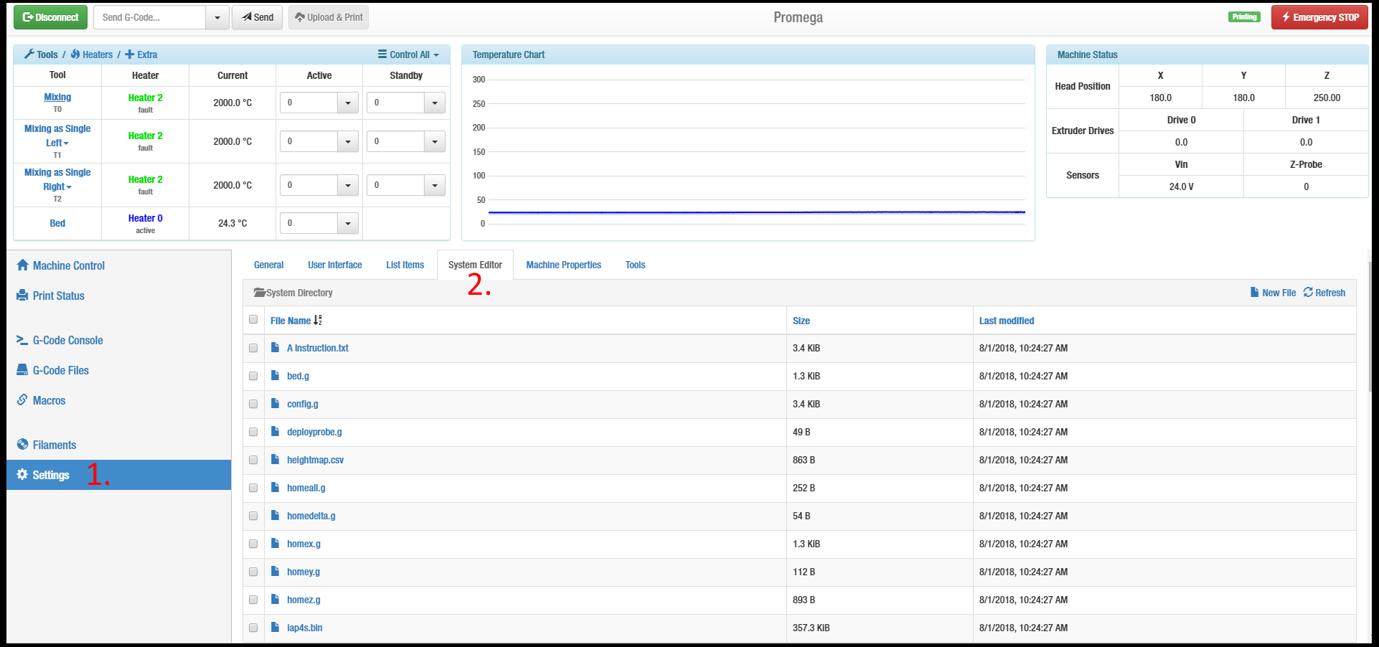
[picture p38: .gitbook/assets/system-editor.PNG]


Look for "machine\_zprobe.g" \(and click\)

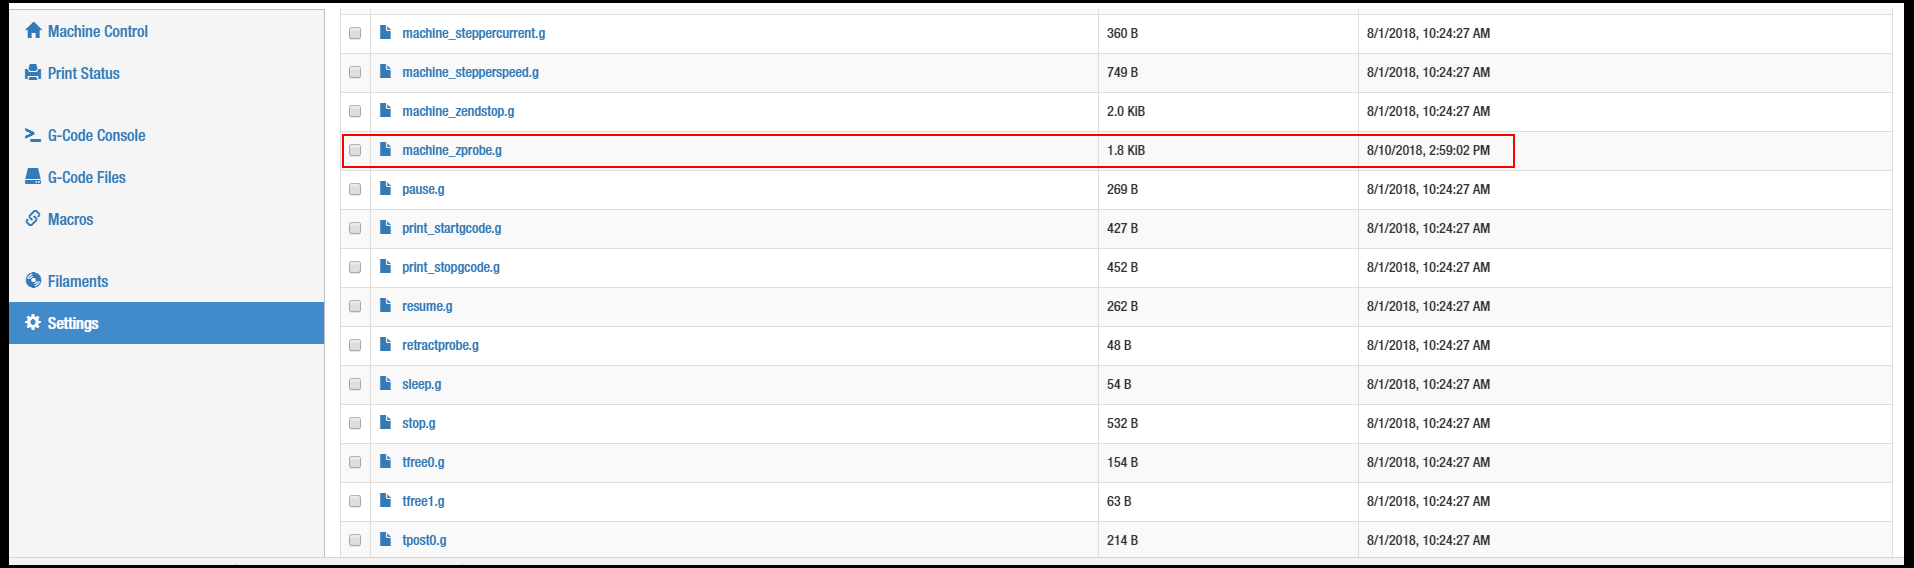
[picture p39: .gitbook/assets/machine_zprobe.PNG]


Go to the last line of code.

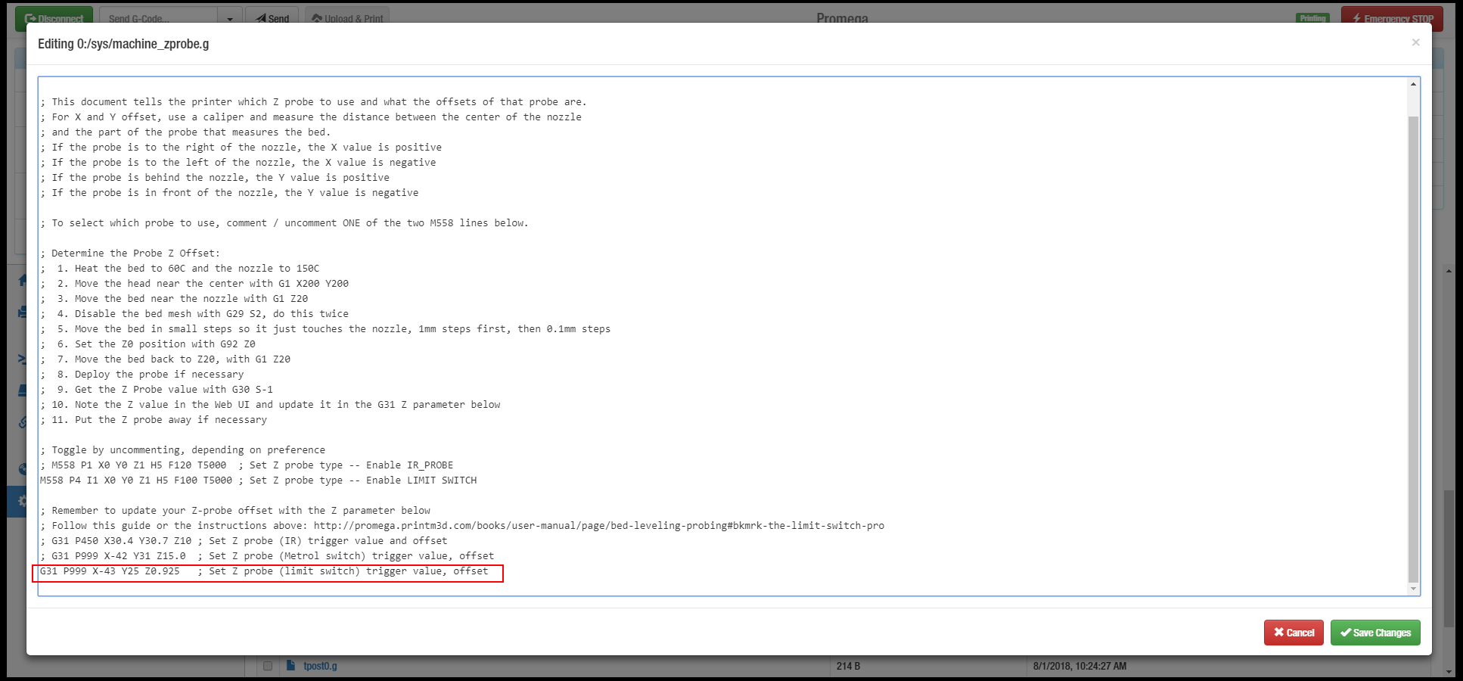
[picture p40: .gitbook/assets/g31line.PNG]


Replace the Z\#\#\# \(e.g. Z0.95\) with your new Z offset number \(POSITIVE ONLY\).

Save changes. 

Done.

## Map The Bed

{% hint style="info" %}
Also known as: _**Bed Compensation**_
{% endhint %}

### Note:

Assumption: Your bed probe has been setup. 

### Home Printer

HOMED

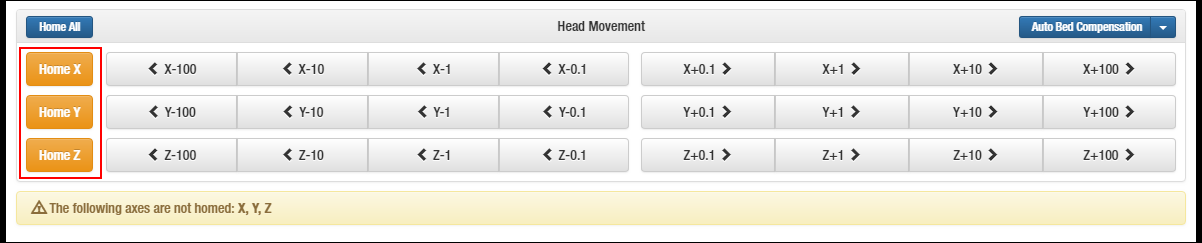
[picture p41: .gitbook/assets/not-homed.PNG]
NOT HOMED


### Heat The Bed

```text
M140 S60
```

### Move Bed To Position

```text
G1 Z15
```

### 

#### Engage Bed Probe

### Probe

```text
G30
```

### Read The Bed

```text
G29
```

Wait for the probing to finish.

Check for any signs of green. 

* There should be some green.
* If not, your bed probe is NOT setup.

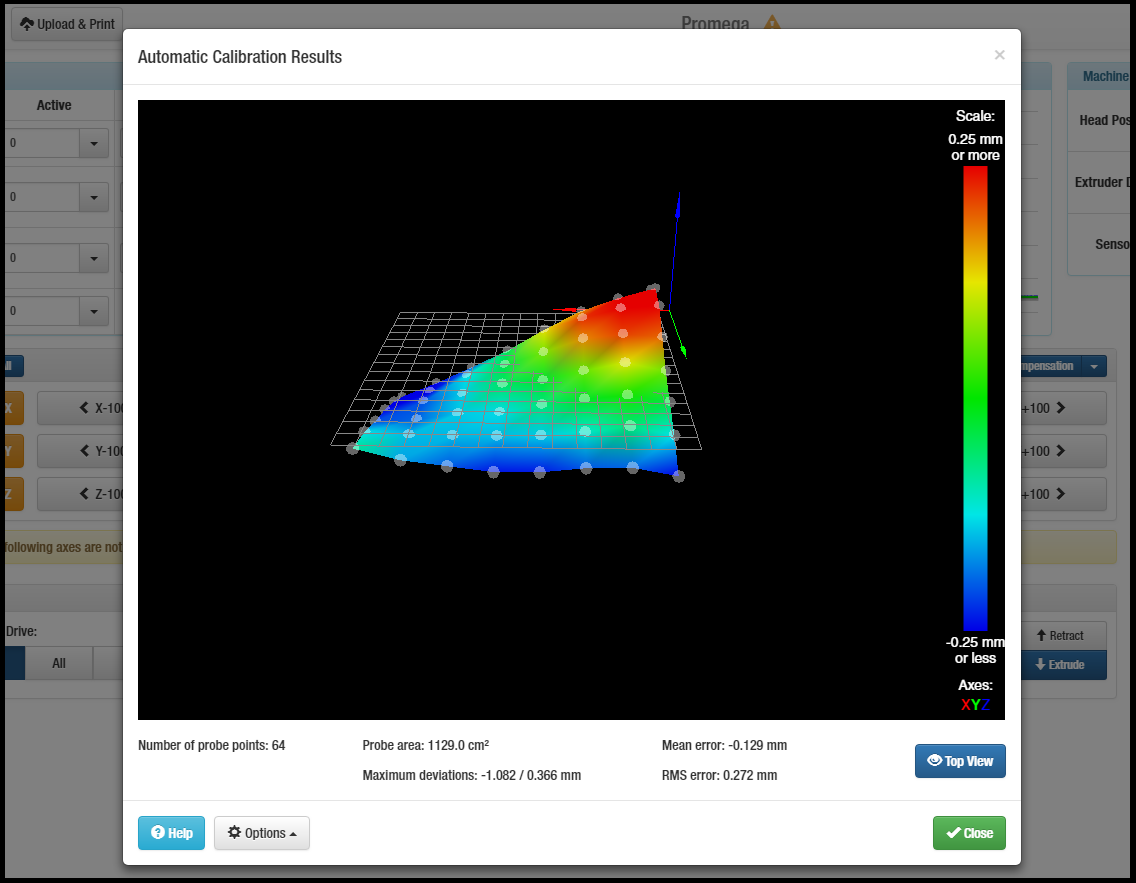
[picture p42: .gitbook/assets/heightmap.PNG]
Example: Proper Use of Mesh Compensation


Click close.

#### Move Bed Away

```text
G1 X187 Y154 Z100
```

### 

### Disengage Bed Probe

You are ready to print.

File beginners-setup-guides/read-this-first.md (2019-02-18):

# Read This First

Before starting the Beginner Guides guides, please complete the following steps to ensure your printer is working properly and is connected to your local network.

1. Read the [Critical Warnings](../getting-started/critical-warnings-and-information.md) in the Getting Started chapter of the Promega. This contains useful and important information about what to do and \(more importantly\) what not to do with your Promega.
2. Follow the [Unboxing & Assembly](../getting-started/unboxing-and-assembly.md) and [Mechanical Check](../getting-started/check-your-printer.md) guides. This will make sure your printer is ready to go.
3. Complete the [Network Setup](../getting-started/setup-your-network.md) guide in order to connect your Promega to your local network.
4. Continue on to the next guide!

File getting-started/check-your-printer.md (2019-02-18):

---
description: >-
  Your Promega has probably had a long journey to arrive at your front door.
  Follow this guide to ensure that your Promega arrived in one piece and is
  ready to print.
---

# Check Your Printer

First of all, check for any nuts and bolts in and around the frame. It is possible that fasteners became loose during shipping.

## CoreXY

### **Belt Routing**

All the belts should be riding on bearings or driven by pulleys. If the belt tension became too low during the trip it is possible that one of the belts moved from its desired place. If you notice a CoreXY belt which is not seated on a bearing or pulley. Follow the [Repairing CoreXY](../repair-and-maintenance/install-uninstall/corexy.md) guide.

### **Belt Tension**

Check the belt tension in the CoreXY, you can do this by feeling the force on the belt as shown in the picture below. The first picture shows a tight CoreXY belt, the second picture a loose belt. Once you release the belt, it should spring back and vibrate. If this does not happen, it might be another indicator of a loose CoreXY belt.

Tight CoreXY Belt

Loose CoreXY Belt

If your CoreXY belt system is loose follow the [Belt Tensioning Guide](../repair-and-maintenance/belt-tensioning.md#corexy-tuning).

## Z-Platform

### Z-sliders

The Z-sliders are 3D printed parts that allow the Z-platform to ride along the four aluminum extrusion on the corners. Check that the Z-sliders are properly seated on the aluminum extrusion.

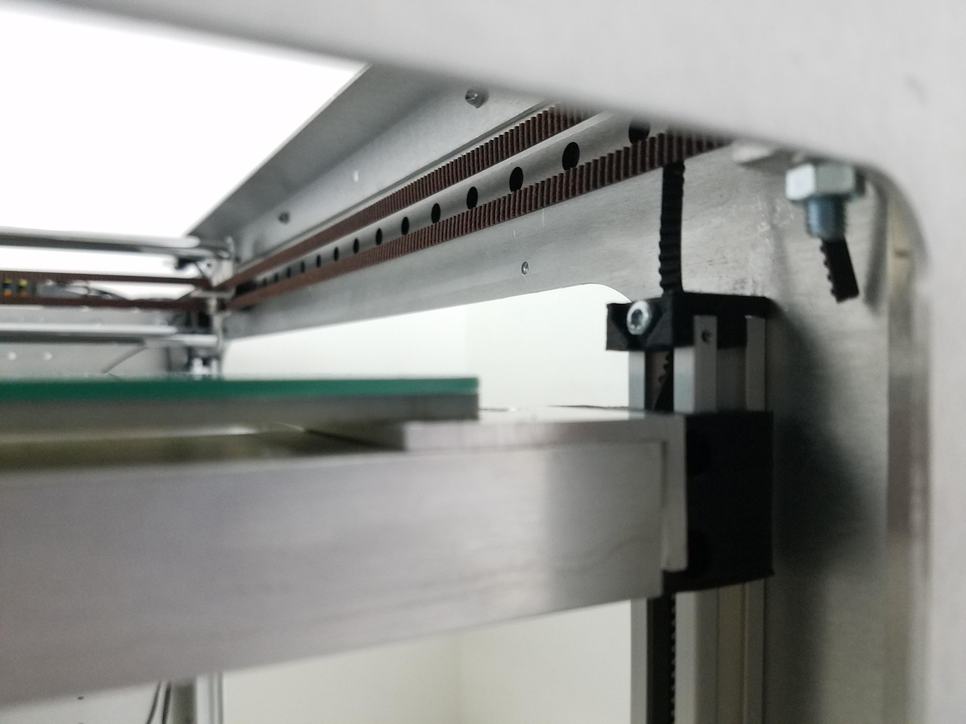
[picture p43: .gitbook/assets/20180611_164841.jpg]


### Lifting the Bed

Next, we will checkout the Z-assembly. During transport it is possible that your Z-assembly became misaligned. If you cannot lift your bed as outlined in the steps below because the bed is too far off level, follow the steps in the [Leveling the Bed](../repair-and-maintenance/mechanical-bed-leveling.md) section.

1. Grab your bed from two points opposite from each-other, as shown in the image below.   
2. Gently and slowly lift the bed up. Never pull up the bed too fast. Remember that moving motors by hand will generate a current and power your printer. While you are lifting the bed you will notice your Cold-section fan spinning. The board can tolerate a significant amount of voltage, but lifting the bed up too fast can fry it.

### **Belt Routing**

Confirm that the belts are properly mounted in the Promega. Check that all four belts are held in place at the bed of the 3D printer by belt clamps or screws. Check that the belts go through the 15x15 aluminum extrusion rail, to the pulley and to the top belt clamps.

### **Belt Tension**

To confirm that the belt tension in each of the Z-sliders is appropriate, feel the tension of the belt tension under the Z-platform as shown in the picture. Pull down softly on the belt in order to feel the tension. You should be able to strum the belts slightly. Try to maintain a similar belt tension between the four different corners.

Feeling the Z Belt Tension

## Cable Chain

Next we will check the cable chain of the Promega. The cable chain should be attached at the back of the extruder on the wiring assembly as well as on the back right of the printer. Check that the cable chain is properly attached on both of these points.



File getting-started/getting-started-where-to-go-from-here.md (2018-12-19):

---
description: What now?
---

# Getting Started: Where to Go From Here

Now that you have completed the Getting Started guides. You are ready to go. Consider reading the following guides as you learn more about the Promega and its functionalities.

* [Duet3D G-code Wiki](https://duet3d.dozuki.com/Wiki/Gcode): All supported G-code commands
* [Duet Maestro Wiring](../documentation/electronics/duet-maestro-wiring.md): Explanation of the Wiring of the Promega.
* [Updating SD Card Structure](updating-sd-card-structure.md): How to update the SD card structure.
* [Macros](../documentation/software-firmware/macros.md): Learn more about macro files and how they can make your life easier.
* [Repair Guides](../repair-and-maintenance/): The chapter that can fix all your problems \(hopefully\).
* [Maintenance Guides](../repair-and-maintenance/): Maintain the printer!

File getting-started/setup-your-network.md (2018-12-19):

# Setup Your Network

## Network Setup

Connecting to your Promega via your local network is very useful as you get access to the Duet Web Console. You can connect your Promega to your local network via the Ethernet port on the Duet Maestro. Once the network settings are properly configured, you should be able to connect to the Duet board and access the Duet Web Console. In order to configure your network settings you will need to edit files on the microSD card. The Promega microSD card has a configuration file called _config.g_ in the _sys/_ folder. This file contains all the necessary information in order to connect to your network.

### First-Time Start-up

If this is your first time starting up the printer, follow this section. The pre-configured Promega network settings, which are loaded onto every SD card when the printer goes out our door, utilize DHCP in order to get an IP address from your router. This should allow your printer to connect automatically to your network. If this is successful, you should be able to enter the machine name into your browser tab followed by a forward slash "/". This could look like this: **my\_promega\_name/**. If you are connecting to your Promega for the first time, you should be able to enter **promega/** into a browser URL textfield in order to connect.

### Configuring Network Settings

If the First-time start-up connection did not work, or you want to set-up your own network settings, you can follow the following section. It is also possible to set a static IP address for your Promega, this will allow you to connect to that IP address to connect to your printer. For example, a static IP address could be the following: _192.168.1.144_ or _10.0.0.214_. However, the type of IP address is dependent on your network. If you are unable to connect your Promega to your internal network by directly connecting an Ethernet cable to the router, follow the Network Bridging section below. Network bridging will allow you to access the Duet Web Console with the Ethernet cable directly connected to your computer.

### Changing the Network Settings via SD

1. Before removing your microSD card from your printer, we recommend you turn off your printer. This reduces the risk of damaging your Duet Maestro. Once the printer is powered off, press the SD card into the board in order to remove it. For more guidance on the SD card check out [this guide.](../documentation/software-firmware/sd-card-structure.md)
2. Insert the microSD card into your computer with the microSD card reader. Open the _machine\_access.g_ file. This file will be in the _sys/_ folder and configures the network settings of your Promega. It is best to open the file with a text editor like [Notepad++](https://notepad-plus-plus.org/download/v7.5.6.html) or WordPad \(Default Windows Accessory\). The default Windows Accessory _Notepad_ is not recommended as it does not separate the G-code commands into individual lines.
3. There are two options for configuring your network: DHCP and static IP. If you utilize DHCP, your network router will assign the control board an IP address. You will then be able to connect to the printer using the printer name you define in the configuration file. **DHCP is the recommended option if you are unfamiliar with networking.** Using a static IP means that you give the Promega a unique and free IP address on your network. You will then be able to connect to the Promega by entering that IP address into a browser tab. Choose the tab below \(DHCP or static IP\) depending on your choice.

{% tabs %}
{% tab title="DHCP" %}
Complete these steps if you want to connect to your Promega using the DHCP option.

a. Open the file _machine\_access.g_ and find the `M550` command located in this file. The `M550` command sets the machine name, this command syntax requires a P parameter before the machine name. Therefore, if you wanted to name your printer _unicorn_ you would type `M550 Punicorn`. Change the printer name to something you prefer, remember this name as you will use it to connect to your printer. By default the machine name is `promega` .

b. Find the `M552` command in the _machine\_access.g_ file. The `M552` command sets your IP address and enables or disables the network. In order to set your network setting to DHCP, the following command should be entered: `M552 P0.0.0.0 S1`. The P parameter allows you to define an IP address, entering `P0.0.0.0` enables DHCP. The S parameter enables \(`S1`\) or disables \(`S0`\) network, because you are setting up your network you should set the parameter to `S1`.

c. Ensure that the other `M552` command is commented out!

Your _machine\_access.g_ file network settings for connecting to a network using DHCP could look like this:

```text
 ; machine_access.g
 ; June 29, 2018

 ; Set the machine name and IP address in here

 M111 S0                       ; Debugging off
 M550 Punicorn                 ; Set machine name, in this case typing unicorn/ would connect you to the printer

 ; M551, No Machine Password
 ; M540 PBE:EF:DE:AD:FE:ED     ; Set MAC address, this can be used to assign a given IP in the DHCP
 M552 P0.0.0.0 S1             ; Use this to enable DHCP
 ; M552 P192.168.1.112 S1     ; This would set a static IP address but it is commented
```

In the example above your machine name would be _unicorn_. Continue to the step below.
{% endtab %}

{% tab title="Static IP" %}
**Static IP Address**  
Complete this if you want to connect to your Promega with a Static IP address.

a. Find the network section in the _machine\_access.g_ file. Find the `M552` command. This command sets your IP address and enables or disables the network. In order to set your network setting with a static IP the following command should be entered: `M552 Pnnn S1`. Where `nnn` is your preferred IP address. Your IP address depends on your local network. It could be in the form of \(_192.168.1.216_ or _10.0.0.216_\). The S parameter enables \(`S1`\) or disables \(`S0`\) network, because you are setting up your network, and want it enabled, you should set the parameter to`S1`.  
b. Choose an IP address on your network that is free. Typically "higher" IP addresses will work, such as `192.168.1.216` instead of `192.168.1.11` . It is best to log-in to your router in order to check which IP addresses are free.  
c.. Ensure that the other `M552` command is commented out!

Your _machine\_access.g_ file network settings for connecting to a network with a static IP address could look like this:

```scheme
 ; machine_access.g
 ; June 29, 2018

 ; Set the machine name and IP address in here

 M111 S0                       ; Debugging off
 M550 PPromega                 ; Set machine name, type promega/ in your browser!

 ; M551, No Machine Password
 ; M540 PBE:EF:DE:AD:FE:ED     ; Set MAC address, this can be used to assign a given IP in the DHCP
 ; M552 P0.0.0.0 S1             ; Use this to enable DHCP, in this case commented
 M552 P192.168.1.112 S1        ; Set Static IP address and enable networking
```

In the example above you should be able to connect to your printer by entering the IP address `192.168.1.112` in your browser tab.

If you want to find out the structure of your internal IP address, open a command prompt on a computer connected to the same network as the promega and enter the command `ipconfig`. \(Open a command prompt by pressing _Windows Key_ + _R_, type _cmd_ and press _Enter_\). This will print your network settings and status, look for the "IPv4 Address" number. That number represents an internal IP address on your network. Of course this IP address is occupied by your computer and therefore not a valid IP address for your Promega! 

Continue to the step below.
{% endtab %}
{% endtabs %}

1. When you have made the necessary changes to your network settings, save the _machine\_access.g_ file and safely eject the SD card. Insert the SD card back into the Duet board. Ensure that the Ethernet cable is connected properly to the Duet board and turn the board back on. It will take a while for your printer to boot and connect to the network \(~30 seconds\). When your Ethernet cable is properly connected to the board, the green LED should be flashing and the yellow LED should be solid.    
2. Once your printer has had the time to start up, open a browser tab on a computer **connected to the same network as the printer**. In the browser URL textfield enter:
   * Your printer name followed by a forward slash "/" if you used DHCP. For example, `unicorn/`, if you named your printer "unicorn" \(nothing wrong with that!\). 
3. If the connection is successful the Duet Web Console should be shown. You have completed the network setup.
4. When you have made the necessary changes to your network settings, save the _machine\_access.g_ file and safely eject the SD card. Insert the SD card back into the Duet board. Ensure that the Ethernet cable is connected properly to the Duet board and turn the board back on. It will take a while for your printer to boot and connect to the network \(~30 seconds\). When your Ethernet cable is properly connected to the board, the green LED should be flashing and the yellow LED should be solid.    
5. Once your printer has had the time to start up, open a browser tab on a computer **connected to the same network as the printer**. In the browser URL textfield enter:
   * Your printer's IP address set in the configuration file with the M552 command. It could look like this `192.168.1.216`. 
6. If the connection is successful the Duet Web Console should be shown. You have completed the network setup.

### **Network Bridging**

If you are unable to connect your ProMega to your internal network it is possible to use the ethernet cable to connect the printer directly to your computer. In order to do this, complete the _Connecting to the Promega via SD: Static IP_ section, remember the static IP you give the printer, but instead of connecting the ethernet cable to your network, connect it to your computer and follow the guide below.

**Windows**

1. Open Network Connections, you can do this by opening the _Control Panel &gt; Network and Internet &gt; Network and Sharing Center &gt; Change adapter settings_

   

2. Once you have the _Network Connections_ window open. Here you will see your network adapters. The ethernet adapter represents your connection to the Duet board. Find your current network adapter, presumably a WiFi adapter. Ctrl + click both the Ethernet adapter as well as the current network you are using. Then right click on one of the selected adapters and select _Bridge Connections_.

   

3. This will create a new Network Adapter called _Network Bridge_. You should now be able to connect to the ProMega with the static IP address you determined earlier. Enter the static IP address into a browser URL textfield.

### Configuring Multiple Devices to the Same Network

If you are adding multiple different Promegas to the network it will change the procedure. This is because a network will require a unique machine name or IP address in order to work.

{% tabs %}
{% tab title="DHCP" %}
If you are using DHCP you will have to give the two different Promegas different unique machine names with the`M550` command. By default the Promega will be called Promega with `M550 PPromega` , so you will have to open _machine\_access.g_ and change the `M550` .
{% endtab %}

{% tab title="Static IP" %}
If you want to configure multiple Promegas with static IP addresses you will have to give the Promegas each a unique IP address that is free on your network with the `M552` command. The machine name does not have to be unique.
{% endtab %}
{% endtabs %}

For additional help connecting to the printer via USB and Network setup, visit the following links:

1. [Duet3D Network Setup](https://duet3d.dozuki.com/Guide/1.%29+Getting+Connected+to+your+Duet/7)
2. [RepRap Firmware G-Code Wiki](http://reprap.org/wiki/G-code)
3. [M3D Support](https://printm3d.com/support)
4. [Duet Forum](https://forum.duet3d.com/): For Duet and RepRap firmware specific questions

## The Web Interface

The Duet Maestro allows control via the Duet Web Console. We highly recommend connecting to your Promega via your network so that you can make use of this! Follow the guide below to learn more about the Duet Web Console. If you have not yet connected your printer to your network, follow the [Network Setup](setup-your-network.md#network-setup) guide.

### The Duet Web Console

Duet Web Console

The web console is divided into two halves. The top half features functions to monitor and analyze the status of your printer. The bottom half focuses on control of your printer and configuring its settings.

#### Status

The status part of the web page indicates various readings to describe the current state of your printer.

#### **Tools & Temperature**

On the left half is a table that allows you to monitor the temperature of the different tools as well as the bed. The temperature readings are important to keep track of. With the table as well as the graph you can keep track of all the temperatures of the components of your 3D printer.A value of 2000 C for any of the components in this table indicates problems with a temperature sensor.

Temperature Readings

By clicking on the text-fields of the tools in the table you can change the temperature of the tools. Press enter to update the temperature. You should see a slow increase in temperature. The _Active_ column represents the temperature of a tool when it is **selected**, the _Standby_ column represents the temperature of a tool when it is **not selected ,** but was previously selected. It is best to have a low standby temperature for a tool, so it does not heat up unexpectedly.

By clicking on the tool names in the _Tool_ column you can change your currently selected tool.



The temperature graph provides helpful insight of the temperature of your tools and bed over time. This can be helpful to spot oscillations in temperature, as seen in the image below, or heater faults and other issues.

Temperature Chart

**Machine Status**

The machine status tab includes the position information of the printer. The head position information displays where the printer currently thinks it is. This is very important to keep track of to minimize the risk of crashing the printer. The X, Y and Z values represent the different axes of the 3D printer. Normal values for these fields are listed below in this table.

|  | Axes Limits |  |
| :--- | :--- | :--- |
|  | Max \(mm\) | Min \(mm\) |
| X - Axis | 388 | 0 |
| Y - Axis | 388 | 0 |
| Z - Axis | 377 | 0 |

The extruder drive values can vary greatly as you perform prints. The voltage in value is helpful as it can help you figure out electrical problems. Optimally it should remain near 24V when none of the printer components are running. The Z-probe value is important as well. This value will change whenever either Z-probe, the limit switch or the IR probe, is toggled. Testing the Z-probe before running probing or leveling commands \(such as `G30`, `G32` or `G29`\) is extremely important and can prevent crashes. When the Z-probe is not toggled the value should rest near 0.

Machine Status

### Control

In order to control your printer, the bottom half of the web console features 6 different tabs on the bottom left side with different features. These tabs allow you to visit different functions of the printer as well as send commands.

**Machine Control**

Machine Control

The Machine Control tab features different buttons in order to control different assemblies of the printer. This feature is helpful to load filament or move the extruder carriage to a specific point in the printer. Be careful with using these buttons as it can crash the printer. Remember the direction that you will send an assembly toward as you press these buttons. Pressing the positive Z buttons will send the bed downward, and pressing negative Z buttons will send the bed up.

**Print Status**

Print Status Screen

The print status tab is helpful when printing. It includes all kinds of information to analyze during a print. Use the Z Baby Stepping window to change the offset of the nozzle to the bed during a print. Use the Speed and Extrusion factors to change the speed and extrusion rate of the print. These settings can be very helpful to get the first layer to stick, but be careful as these settings can damage your print quality. Use the pause button to temporarily stop the print. Once you pause the print you can resume or stop the print. This screen will also display other statistics during a print such as layer time and length of filament used.

**G-Code Console**

G-code Console

The G-code console is a vital to an experienced 3D printing user. This tab allows you to enter any RepRap Firmware supported command. The printer will execute any command entered here and print feedback and errors. Visit the [RepRap Firmware G-Code](https://reprap.org/wiki/G-code) website to learn more about all possible G-codes. Be careful when entering G-code commands as the printer will execute whatever you command you send it.

**G-code Files**

G-code File Screen

This tab is used to upload G-code files to the Duet board. Use the _Upload G-code File\(s\)_ button in order to upload a _.gcode_ file to the printer in order to print it. Click on an uploaded file in order to print it. You also have the ability to create directories here in order to organize your files. This is a great idea if you have a 8Gb microSD card.

**Macros**

Macros Screen

User defined macros are stored in this tab. Use the dark-blue _Upload Macro File\(s\)_ button to upload _.gcode_ macro files. Macros are useful when you find yourself repeatedly performing a sequence of G-code commands. You can easily put these commands into a macro file and upload it here. Click a macro file in order to execute it.

**Filaments**

Filaments Screen

Utilize this tab in order to define printer filament settings. This can also be performed in Slicer Software.

**Settings**

Settings Screen

**This tab is one of the most important**. This tab allows you to change the _sys/_ directory in your SD card and define other user settings. Whenever the guides in the future reference a change that is necessary to the system files such as _config.g_ or a _machine.g_ file, you can change the files in the settings tab. The Settings tab includes more tabs:

* General: Includes firmware and web console information
* User Interface: Change the look and feel of the Duet Web Console
* List Items: Includes web page suggested options
* System Editor: A very useful tab to change files in the _sys/_ directory of your microSD card. **You will find the** _**config.g**_ **file here as well as other system G-code files.**
* Machine properties: Defines properties of the different drives \(motors\) of the printer.
* Tools: Defines the properties of the tools.

### Additional Resources

* Duet3D Wiki: [Duet Web Control Manual](https://duet3d.dozuki.com/Wiki/Duet_Web_Control_Manual#main)
* [Duet Web Control GitHub Repository](https://github.com/chrishamm/DuetWebControl)

Continue on to the [Updating SD Card Structure](updating-sd-card-structure.md), the next chapter in the [Getting Started](./) guide.

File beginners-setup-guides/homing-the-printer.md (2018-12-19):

# Homing The Printer

Before you start printing or moving any component of the Promega, we recommend homing the printer. Follow the steps below in order to home your printer. Prior to homing your printer check that the gantry and bed are able to move freely and access the limit switch. This guide assumes you have connected to the Promega as outlined in [Network Setup]().

### Printer Axes



In order to control the Promega it is important to understand the axes of the printer and their orientation. As you can see in the image above the X axis spans across the front of the printer from left to right if you are facing the front of the printer. The Y axis is pointing from the front to the back and the z-axis is pointing down. Remember these axes directions as you jog the printer with the _Machine Control_ tab in the [Duet Web Console](). 

{% hint style="info" %}
**Positive Z is DOWN**

**Negative Z is UP**
{% endhint %}

The origin of this coordinate frame is in the top-front-left corner of the printer. This can be seen at the intersection of the three red axes of the 3D printer in the image above.

### The Homing Process

Follow the steps below to correctly home your printer.

#### Checking the path

To ensure that the printer homes correctly, we recommend moving the CoreXY gantry manually to the limit switches located in the back right corner when the motors are not powered. If you need to power down the motors you can use the G-code command `M84` to stop the idle hold of the motors. Watch out as this will disable **all** motors, and could cause the bed to drop. Remove all items from inside of the printer before homing. The PTFE filament tubes on the extruder carriage cable assembly should be clicked in place \(shown in the image below\), or they could cause problems when homing the X-axis.

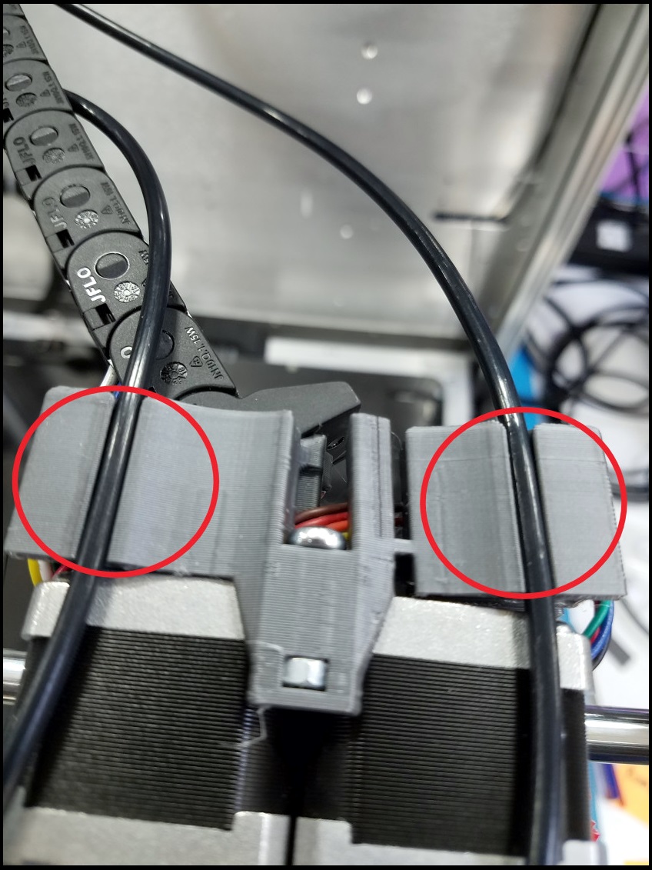
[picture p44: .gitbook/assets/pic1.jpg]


Move the coreXY gantry against the Y-limit switch, listen for the click of the limit switch. 

{% hint style="warning" %}
Be careful not to move the extruder carriage past the limit switch tab.

It could break off.
{% endhint %}

Then move the coreXY gantry against the X-limit switch.

Make sure the bed is resting on the Z-limit switch and that there is nothing underneath the bed.

### Homing the Printer

{% hint style="info" %}
We recommended you tune the Z homing of the printer:

Once after receiving of your Promega.

AND

Any time you make changes to the relative distances of the bed and the nozzle 

* Bed glass installation
* Nozzle replacement
* Extruder swap \(K'Tana vs. Compound\) 

See details on this process at [Tuning the Z Homing Procedure](homing-the-printer.md#tuning-the-z-homing-procedure).
{% endhint %}

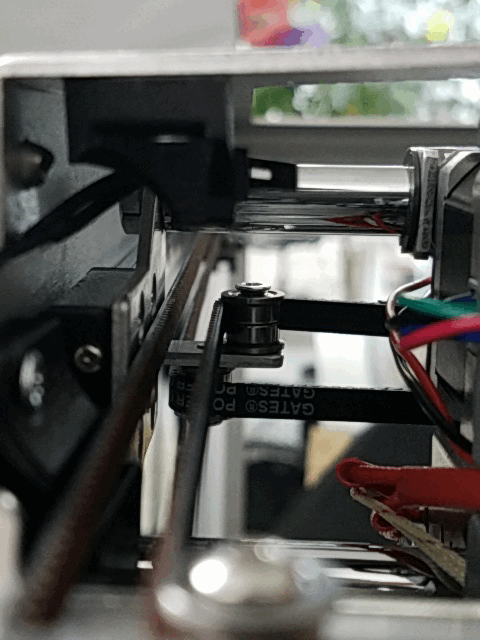
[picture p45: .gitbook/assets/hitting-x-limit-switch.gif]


You are now ready to home the printer. There are multiple ways to initiate the homing process. You can press the _Home All_ button located in the _Machine Control_ tab of the Duet Web Console. You can also send the G-code command G28. These two operations will both execute the same file _homeall.g_, located on the microSD card.

The CoreXY gantry should move toward the Y-limit switch located at the back of the printer first. Once it has hit that limit switch, it will move toward the x-limit switch. Next, the bed will lift itself up and back down slowly, until it has hit its limit switch.

Now all axes are homed. Remember that your motors are now powered and you will not be able to move any of the assemblies by hand. Use the `M84` command to temporarily disable idle hold current on your stepper motors, allowing you to move the motors. Your \(0,0,0\) is located at the top-front-left of the printer. 

### Tuning the Z-homing Procedure

**Because the distance between the bed and the nozzle depends on your Promega configuration \(K'tana vs. Compound, Glass vs. no glass\). You will have to tune** _**machine\_zendstop.g**_ **for Z0 to line up.**



Ideally whenever you home the printer and send the command `G1 X0 Y0 Z0` \(telling the printer to go to \(0,0,0\)\) the print bed will touch the nozzle. However, as outlined above, the difference between the bed and the nozzle varies depending on your setup. 

#### Follow the steps below to update your _machine\_zendstop.g_ file.

Home the printer if you have not already done so in the section above.

Send the command

```text
G29 S2
```

This will disable bed leveling. Bed leveling can conflict with your homing value.

Move the printer to Z10 with the command

```text
 G1 Z10
```

Move the printer head to the center with

```text
 G1 X200 Y200
```

Jog the bed up the nozzle with the buttons in machine control until the bed is touching the nozzle. Use the _Z1mm_ and _Z0.1mm_ buttons. Remember that you are about 10mm away from the nozzle.

Once the bed is properly touching the nozzle record the Z-value in _Machine Status_ on the Duet Web Console_._ 

{% hint style="info" %}
This value will be used in the next step.
{% endhint %}

Open the _machine\_zendstop.g_ file in the _Settings_ tab of the Duet Web Console. This file is called during the homing process of the Z-axis. Find the `G92` command at the end of the file. This command sets the z-axis height.

Update this value with the following formula:

$$
new value = OldValue - SavedValue
$$



#### For example: 

If the _machine\_zendstop.g_ file currently contains the command

```text
G92 Z376.4
```

and I obtained a value of -0.6. 

My new value would be 377mm: 

$$
377= 376.4 - (-0.6)
$$

I would remove the current command and enter:

```text
G92 Z377
```

Save the file.

#### Next Step

Open the _machine\_axisdimension.g_ file in the _Settings_ tab of the Duet Web Console. This file defines the minimum and maximum dimensions of each axis and will be affected by changes to the z-axis end stop.

Find the second `M208` command at the end of the file.The one that says `Set axis maxima` in the comment.

Change the Z value to be the Z end stop value determined above, rounded up to the next integer. 

#### **For example:**

 If the Z end stop is _**376.4**_, the maximum Z needs to be _**377**_.

If the Z end stop is _**377.2**_, the maximum Z needs to be _**378.**_

If the Z end stop is _**379.0**_, the maximum Z needs to be _**379**_ \(no rounding\).

**Save the file and home the printer again.** 

{% hint style="warning" %}
Although you should now be able to enter the command `G1 Z0`, I don't recommend it. 
{% endhint %}

**Manually jog your bed to the nozzle again to ensure that Z0 is when the bed is touching the nozzle.**

Continue on to the next phase: [Get Your Bed Ready](get-your-bed-ready.md).

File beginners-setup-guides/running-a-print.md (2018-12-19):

# Running A Print

Running a print is best done using the Duet Web Console. To connect to your Duet via a network, visit the [Network Setup]() guide. For an introduction on the Duet Web Console visit the [Accessing Web Interface]() guide.

This guide assumes you have properly configured your printer with all the previous guides. That means:

* You have homed all axes of your printer
* You have configured your Z-probe offset
* You have run and enabled mesh bed leveling
* You have loaded filament into the extruder

## Uploading the Print

In order to print something from the Duet board you must first upload the print to the Duet Board. This can be done via the Duet Web Console or by ejecting the SD card and uploading it with a computer. 

**Uploading a print via the Duet Web Console is the easiest way**. 

{% hint style="info" %}
To print on the Duet board your print must have a _.gcode_ file extension. 

To create a G-code file you must slice a model with a slicer. Look at the [What is Slicing?](../advanced-setup-guides/what-is-slicing.md) guide for guidance on how to create a _.gcode_ file.
{% endhint %}

### **Uploading via Duet Web Console**

The Gcode Upload Button

First, we will have to upload the G-code file we produced in the previous guide. 

Connect to the Duet Web Console on the printer. 

Then, press the _G-code Files_ button and then press the _Upload G-code File\(s\)_ button as shown in the image above. This will open a window which will allow you to select the G-code file you sliced. 

_Open_ your preferred file and wait for it to upload.

### **Uploading via microSD**

Power off your printer with the blue power switch.

Remove your microSD card from its slot on the Duet board by pressing it into the board. 

{% hint style="warning" %}
Be careful as the microSD slot on the board is fragile.
{% endhint %}

Insert the microSD card with microSD card reader into your computer.

Open up the drive and select the folder _gcodes_. Upload all the _.gcode_ prints you want into this folder.

When this has completed, safely eject the card and insert it back into the Duet board.

Power on the printer and reconnect to the Duet Web Console. 

You should now be able to see all your prints in the _G-Code Files_ tab on the console \(shown in the image above\).

## Printing the File

Once the file is uploaded, you can click the file in order to print it. A window will pop-up confirming that you are about to print something. Click _Yes._



## Monitoring Prints

Once you have selected a file to print it you can view the prints progress in the _Print Status_ tab.



With various buttons on this screen you can manipulate your print. This can help in certain cases.

### Speed Factor

Change the print speed with the _**Speed Factor**_ ****slider, on the right. This can be helpful to slow down your print during tricky parts, such as the first layer. 

### Z Baby stepping

With the _**Z Baby Stepping**_ buttons you can change the height of the Z during a print. This is very helpful to improve first layer stick during a print. 

### _Extruder Factors_

_**Extruder Factors**_ sliders can be used to change the flow rate of the extruders. 

{% hint style="warning" %}
Exercise caution when using these controls, improper use can quickly ruin your print.
{% endhint %}

### Print Statistics

Aside from these controls the Duet Web Console displays, a heap of cool statistics such as Layer time and length of filament required. 

{% hint style="info" %}
Remember that these statistics are estimates!
{% endhint %}

### Pause

At any point during a print you can pause the print with the orange _**Pause Print**_ button. This will execute a file on the microSD card called _pause.g_. 

This will remove the extruder head from the print, and retract filament but keep the temperature steady. 

You will then be able to execute G-code commands. 

{% hint style="warning" %}
Be careful as you can easily damage your print and printer if you move the extruder into the print. 
{% endhint %}

### Resume

Whenever you want to continue printing you can press _**Resume**_. This will execute _resume.g_. 

### Cancel

If you want to stop your print, you can press the _Cancel_ button. This will execute _stop.g._

This file is also called at the end of a print.

Continue on to the phase: [Common Terminology](common-terminology.md).

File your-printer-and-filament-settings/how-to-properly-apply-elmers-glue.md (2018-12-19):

# How To Properly Apply Elmer's Glue

A guide on how to apply Elmer's Glue properly.

#### Let's begin.

Heat the bed to 70 C.

{% hint style="info" %}
Wait for the bed to reach temperature.
{% endhint %}

Lightly apply a THIN layer of Elmer's glue.

The lines applied showed by all consistent \(either horizontal, vertical, or diagonal\)

{% hint style="warning" %}
Do Not make crazy lines.
{% endhint %}

Wait for the layer to dry.

{% hint style="info" %}
The purple tint of the glue will fade away.
{% endhint %}

Repeat: Apply another THIN layer of Elmer's glue.

You should repeat the THIN layer application until you've done 5 layers.

Thanks to _**m3rc**_ for figuring this out.

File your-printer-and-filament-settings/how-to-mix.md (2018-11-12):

# How To Mix

There are two ways to mix:

**Through the Duet Web Control \(DWC\)**

AND/OR

**Cura Melt Plugin**

## Duet Web Control \(DWC\)

Go To G-Code Console

Run 

```text
M567 P# E#:#
```

P\# = Tool Number

E\#:\# = Mixing Ratios \[ LEFT FILAMENT \] : \[ RIGHT FILAMENT \]

{% hint style="info" %}
Heres a link to the[ Duet3D Documentation on M567](https://duet3d.dozuki.com/Wiki/Gcode#Section_M567_Set_tool_mix_ratios)
{% endhint %}

#### 

#### Example

```text
M567 P0 E0.5:0.5
```

P0 = Tool 0

E0.25:0.75 = 25% of Left Filament : 75% of Right Filament 

## Cura Melt Plugin

Under Construction

{% hint style="info" %}
Here's a link to the [Cura Melt Plugin](https://github.com/PrintM3D/MELT)
{% endhint %}

Thanks to _**gargansa**_ for developing the plugin.

## Voxelizer

Coming Soon.

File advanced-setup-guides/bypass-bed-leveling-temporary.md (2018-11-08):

# Bypass Bed Leveling \(Temporary\)

This guide should be used under these certain conditions:

{% hint style="info" %}
You understand this leveling method is FAST and TEMPORARY. The leveling will be undone after a Z homing, Home All, or power cycle. 
{% endhint %}

{% hint style="info" %}
You want to avoid mesh compensation or Z endstop calibration troubleshooting.
{% endhint %}

{% hint style="info" %}
Your print is small or medium sized.
{% endhint %}

#### 

#### Let's get started.

Physically level the bed. Follow the [Mechanical Bed Leveling](../repair-and-maintenance/mechanical-bed-leveling.md) guide.

Home your X and Y only.

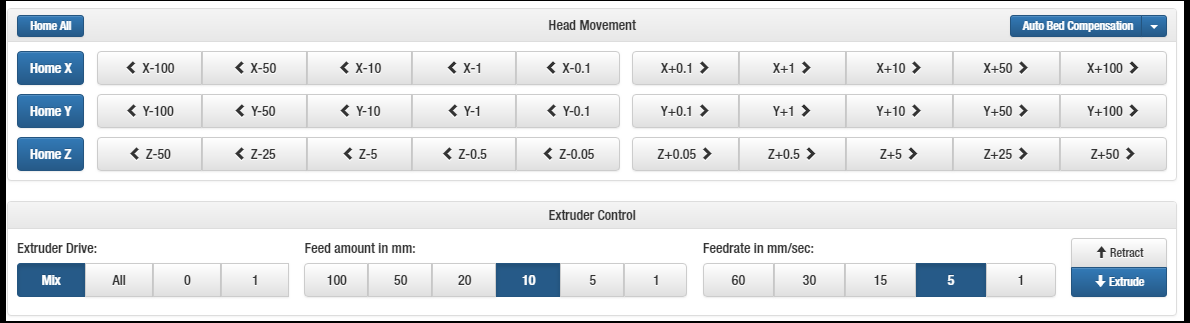
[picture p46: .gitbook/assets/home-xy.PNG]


Move your extruder to the region you will print on. 

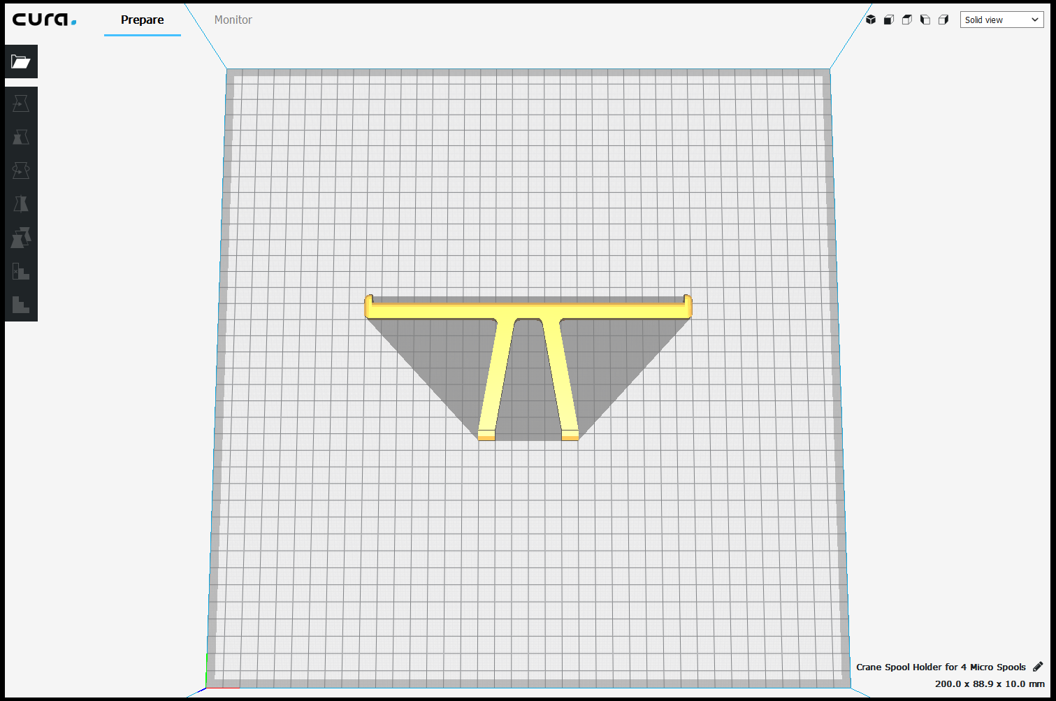
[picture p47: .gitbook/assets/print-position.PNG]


Enter

```text
M564 S0 H0
```

```text
G29 S2
```

```text
M290 R0 S0
```

{% hint style="info" %}
None of the codes above have any movement involved. 

Make sure they are executed
{% endhint %}

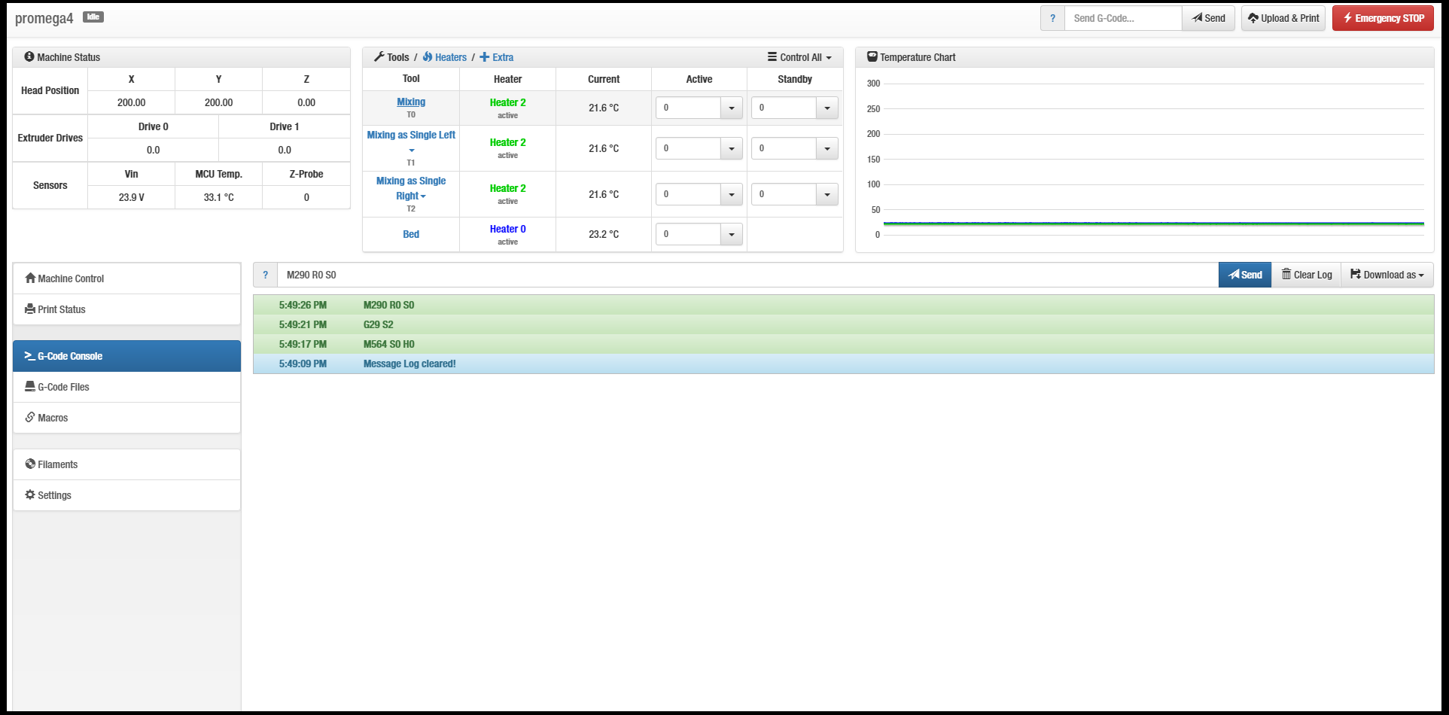
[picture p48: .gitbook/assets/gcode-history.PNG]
Shows a history of executed codes.


Heat your bed to desired temperature.

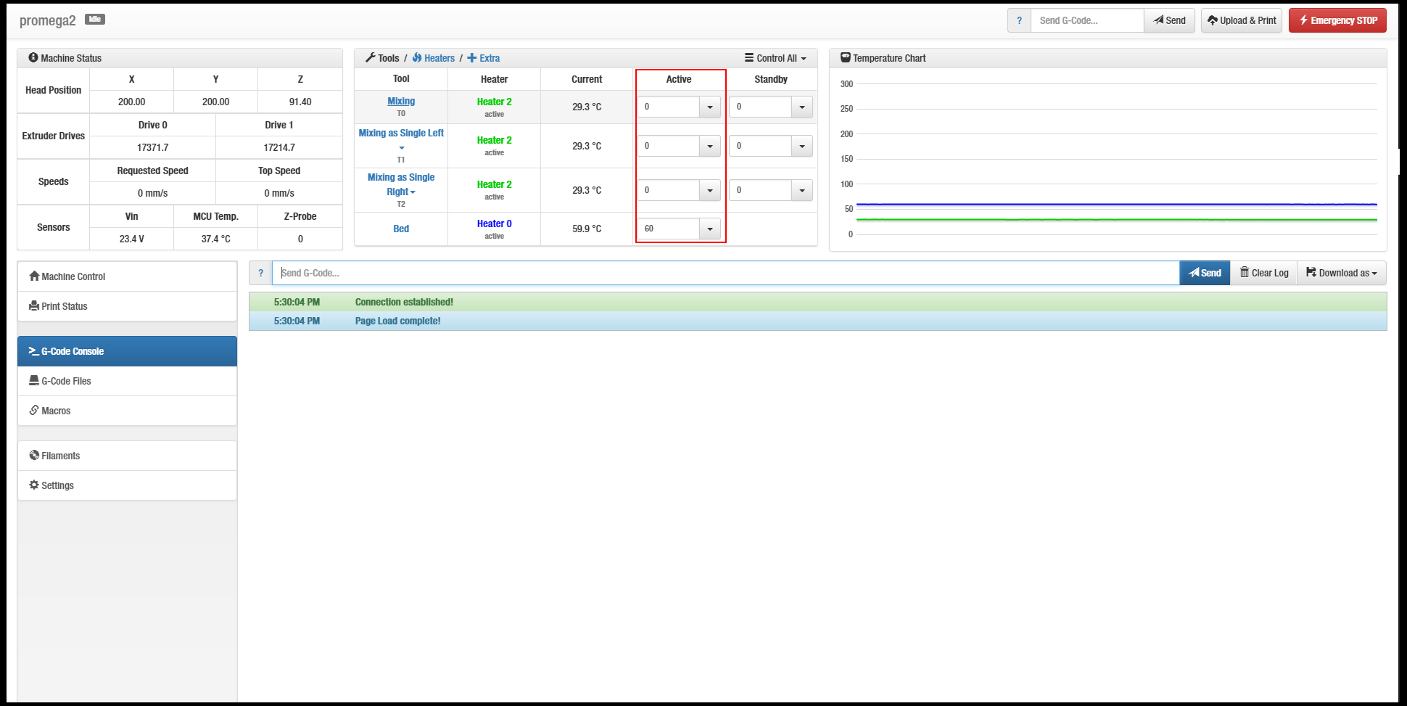
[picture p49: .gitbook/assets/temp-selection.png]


Move the bed until is it paper-width apart from the nozzle. 

{% hint style="info" %}
Paper-width should have mild resistance when moved around.
{% endhint %}

Enter

```text
G92 Z0
```

Check your z position value is set to 0.

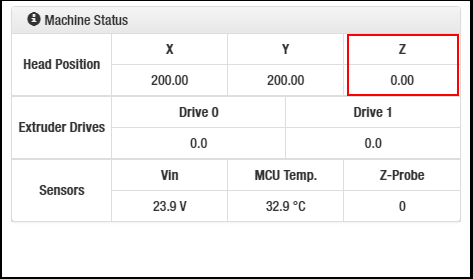
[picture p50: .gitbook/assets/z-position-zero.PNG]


Start your print.

{% hint style="warning" %}
Make sure your print DOES NOT have 

ANY homing commands \(e.g. G28\)

OR 

ANY reference to `M98 Pprint_startgcode.g`
{% endhint %}

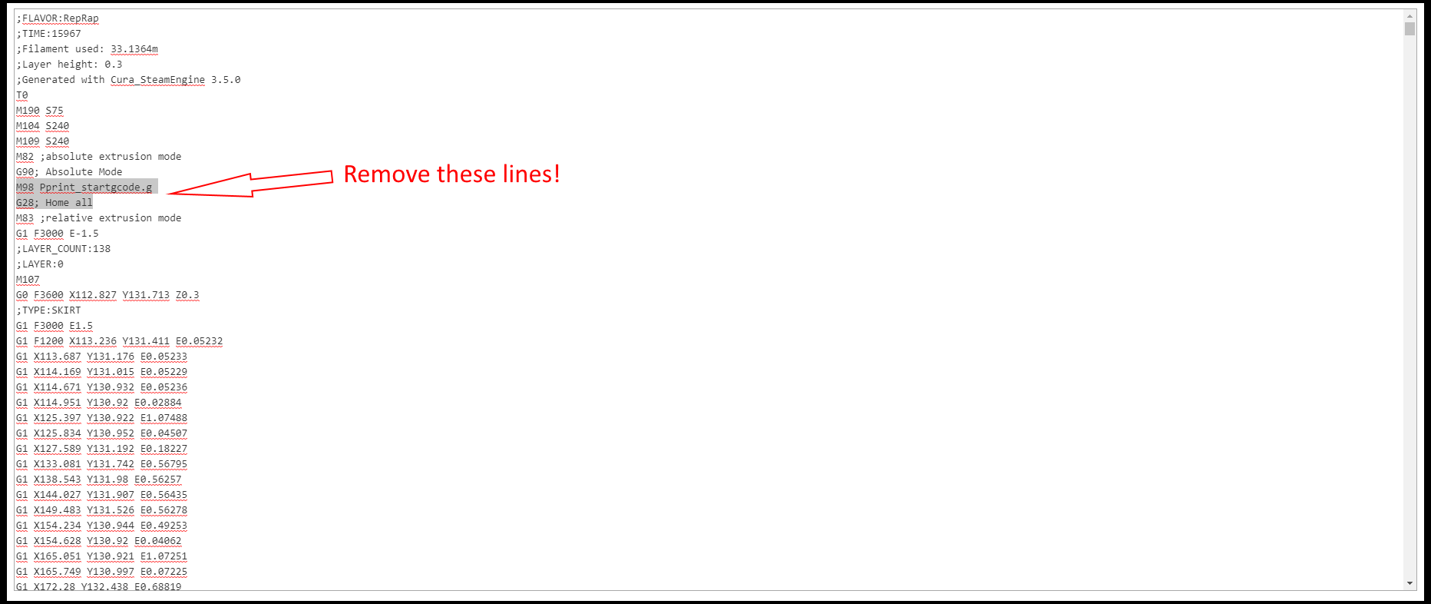
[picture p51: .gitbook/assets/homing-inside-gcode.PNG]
Highlighted lines are homing lines.


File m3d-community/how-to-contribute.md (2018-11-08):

# How To Contribute

This page serves as a future place for community guides. If you have a great idea, procedure or guide that you want to share. 

Create a pull request on the [M3D Promega Docs repository](https://github.com/PrintM3D/Promega-Docs).

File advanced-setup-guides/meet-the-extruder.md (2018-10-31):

# Meet The Extruder

Next, we will move on to one of the most important assemblies on the Promega, the extruder! This complicated assembly can reach temperatures above 300°C in order to melt plastic and print it. 

The extruder assembly contains a fan directly on the front, this is called the _Cold-Section Fan_. It is meant to keep the extruder block, directly behind it, cold. 

{% hint style="warning" %}
If the extruder block gets too hot, filament could start melting before the filament ever reaches the nozzle. 
{% endhint %}

Next, there are two smaller fans called _Nozzle Fans_. These are meant to cool any filament that is pushed out of the nozzle so that it becomes rigid. 

On the right of the nozzle fans is a small electronics board called the _IR Probe_. This probe uses Infra-Red rays in order to detect the bed. 

On the left of the extruder is a small deploy-able limit switch, this is also a Z-probe. Z-probes are used in order to measure the exact distance from the nozzle to the bed. They are also used in order to level the bed of the printer as printing requires a very flat and level surface.

 You can view the image below to see a diagram of the different extruder components.

Extruder Diagram

## Tools

Tools are a relatively new concept in 3D printing. They allow you to create different extruder configuration ahead of time that you can quickly switch between while printing. 

The Duet Maestro board uses tools in order to allow printing with multiple extruders, or mixing extruders. The Promega actively makes use of this in order to print with:

* _**Compound Mixing**_: Different tool mixing ratios
* _**Single K'Tana**_: Dual nozzle prints 

You can find your currently configured tools in the Duet Web Console in a table labeled: _Tools/Heaters/Extra_ on the top-left.

Single K&apos;Tana Tools &amp; Heaters

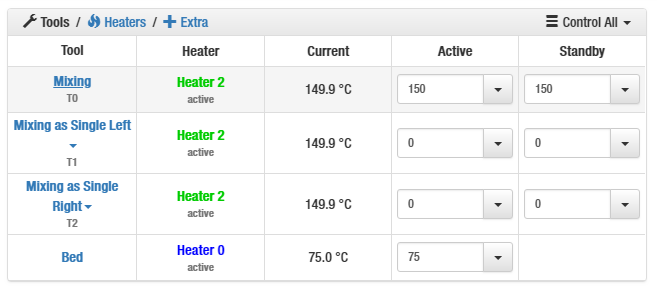
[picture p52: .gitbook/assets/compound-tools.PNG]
Compound Mixing Tools &amp; Heaters


In the image above there are two different tools. 

### What is a Tool?

In RepRap firmware, tools are defined as `Tnnn`, where `nnn` represents a tool number. In the image above there are tools T0 and T1. Each tool has it's own extruder motor attached to it, or multiple if you are mixing. 

A tool also has one heater attached to it. All these tools are defined and configured when the printer powers up with G-code commands, we will go over how exactly that works later. 

### Tool Setups

Below are the default tools for the Compound and K'Tana setups. In order to select a tool you can either click on the tool name in the Duet Web Console or you can send the command `Tnnn` where `nnn` represents the tool number. 

If you wanted to switch to tool 0, you would send the command:

```text
T0
```

The Duet Web Console always shows you which tool is selected: it will underline the tool name. In the image above T0 is selected.

#### Compound Tools:

* `T0`: Mixing tool
  * Extruder 0 \(Left\) & Extruder 1 \(Right\)
  * Heater 2
  * Allows for extruding two filaments and combining them at a 1:1 ratio
* `T1`: Single Left
  * Extruder 0 \(Left\)
  * Heater 2
  * Extrudes with only the right extruder
* `T2`: Single Right
  * Extruder 1 \(Right\)
  * Heater 2
  * Extrudes with only the left extruder

#### K'Tana Tools:

* `T0`: K'tana Single Left
  * Extruder 0 \(Left\)
  * Heater 1
* `T1`: K'tana Single Right
  * Extruder 1 \(Right\)
  * Heater 2

In the future, if you find that none of your extruders are working, or an extruder you didn't expect to be running is running, chances are you have the wrong tool selected. Use the `Tnnn` command in order to select a tool with number `nnn`.

## Filament Properties

There are many different filament types used in the 3D printing industry, a [Google search](https://www.google.com/search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) will prove that. They vary in material, diameter and many other properties. 

#### The Promega allows you to print with 1.75mm diameter filament. 

The Promega can also print many different materials, but if you are a beginner we recommend ABS-R or PLA. These two materials tend to be easiest to print with. 

 Printing temperature varies greatly depending on what material you are printing with.

{% hint style="info" %}
 Please do appropriate research before attempting to extrude a new filament. 
{% endhint %}

#### For example:

PLA prints well at around _**200°C**_ 

ABS-R prints well at around _**230°C**_

Follow the section below in order to get started with extruding.

## Loading Filament

To load filament into the extruder, you will need to find two small holes on the top of the extruder assembly. 1.75mm diameter filament can be loaded into this opening.

Where to Load Filament in the Extruder

It will then be grabbed by the extruder motor and pushed down into the hot-end. 

{% hint style="info" %}
The hot-end term refers to the pieces of the extruder which will heat up in order to melt the plastic. 
{% endhint %}

In the Promega's case, that is the nozzle and the aluminum block surrounding it. Once the filament is melted in the hot-end it will come out of the nozzle. 

### Compound Mixing Loading

The compound nozzle will have two holes to allow entry to two different filaments. It then melts both filaments and combines them to produce one stream of filament coming out. 

### Single K'Tana Loading

The K'Tana has two different nozzles and therefore each filament will get extruded out of separate nozzles. 

### How To Load

To load filament,  follow the steps below.

Move the extruder to the center of the printer by entering the command:

```text
G90
```

```text
G1 X200 Y200
```

Next, heat up the nozzle. 

There are multiple ways to heat up the nozzle to your desired temperature. Use the:

G-code Commands \([move to here](meet-the-extruder.md#loading-filament-g-code)\)

OR

 Duet Web Console \(continue on\)

{% hint style="info" %}
Heating up tools with the Duet Web Console is the easiest. 
{% endhint %}

In the table _Tools/Heaters/Extra_ on the Duet Web Console, enter the desired temperature in the circled box below \(your _Current_ reading should not have a value of 2000°C, 2000°C is an error value\). 



Once you have entered the temperature press Enter. You should now see a steady rise in temperature in the _Current_ box and on the graph to the right. 

{% hint style="info" %}
The temperature you set should depend on the filament you are planning to extrude.
{% endhint %}

Once the extruder has reached it's set temperature you are ready to load your filament. 

Take the filament and insert it into the opening circled in red in the image.

Where to Load Filament in the Extruder

For a _**Compound Mixing  nozzle**_, you will have to load filament into _**both openings**_ in the extruder. 

For a _**Single K'Tana nozzle**_, you will only have to load filament on _**one opening**_ in the extuder. 

Now, on the Duet Web Console go to the _Machine Control_ tab in order to move the extruder motors. In this tab there is a box called _Extruder Control_. 

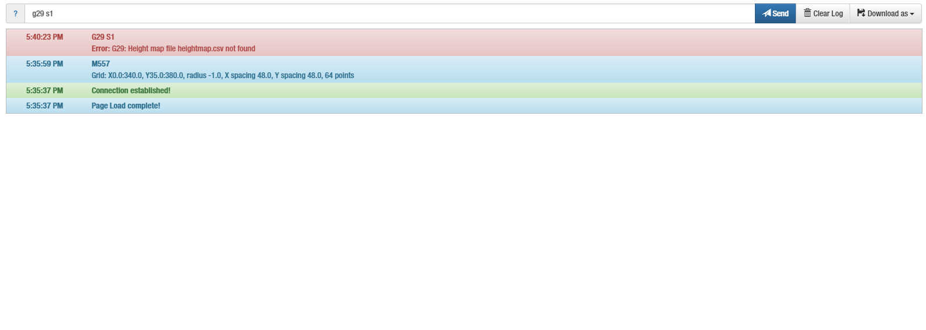
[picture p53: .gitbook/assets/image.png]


Here you can select the extruder you want to control and how much filament you want to extrude and at what speed. 

If you have the _**Compound Mixing nozzle**_, set the _**Extruder Drive**_ settings to _**Mix**,_  in order to get both extruder motors to push filament. 

If you have the _**Single K'Tana nozzle**_ , set the _**Extruder Drive**_ settings to _**Drive 0 or 1**_, depending on which side you loaded filament into. 

The _Feedrate amount_ should be set to 10mm and the _Feedrate_ to 5mm/sec. You can then press _Extrude_ this should move the filament into the extruder. It could be possible that you have to push the filament properly into the opening until the extruder grabs it.



Once the filament is inside the extruder keep pressing _Extrude_ until filament comes out of the nozzle. You can increase the _Feed amount_ to 50mm or more to decrease the times you have to press _Extrude_.

#### Congratulations!

You have just created your first print! It probably looks like a long stream of filament, but that counts, right? 

You can keep pressing the _Extrude_ button for as long as you like, or you can move on to the next section.

## Loading Filament \(G-Code\)

The steps that you accomplished above in order to extrude filament can also be done with G-code commands. Follow the steps below in order to learn more G-code commands.

1. Select your appropriate tool with `Tnnn`. For example, tool 0 with `T0`.
2. Turn off the heat to your tool by sending the command `G10 Pnnn S0`. `G10` allows you to set a tool temperature. The `P` parameter and `nnn` represents your tool number that you want to change the temperature of. `Snnn` is the temperature of the tool. So by setting the temperature to 0 the tool is turned off.
3. If you wanted to turn the temperature of a tool back on you would have to enter the command `G10 P0 Snnn` where `nnn` is your new tool temperature. The `G10` `S` parameter only sets the **active** temperature of a tool. This means the tool will only go to that temperature when it is selected or active.
4. If you wanted to extrude 100mm of filament at a feedrate of 20 mm/sec you could enter the commands below. Remember that you should zero your extruder first before telling your extruder to move. This is because your extruder could have a very high position in mm, for example 10291mm. If you then tell the extruder to move to the absolute position of 100mm. The extruder will have to travel 10191mm backwards, and that will take a long time! You can also turn on relative extruder moves with `M83`, and then you would not have to zero the extruder as it just adds 100mm to the position the extruder is already at.

```text
G92 E0
G1 E100 F120 ; Remember that Feedrate is in terms of mm/min!
G92 E0
```

```text
M83 
G1 E100 F120
M82
```

To retract, pull filament back into the extruder, send a negative extruder position. Like `G1 E-100 F3000`.

## Alternative Commands to Heat

Throughout your printing career with the Promega you will notice other commands to heat up your nozzle. `M104` and `M105` can also be used to heat up your tools.

`M104 Snnn`: Heat up your active tool to `nnn`°C.

`M109 Snnn`: Heat up your active tool to `nnn`°C and wait until temperature is achieved.

`M140 Snnn`: Heat up your bed to `nnn`°C.

`M190 Snnn`: Heat up your bed to `nnn`°C and wait until temperature is achieved.

There are even more commands to heat up your extruder. The `G10` command allows you to heat up any tool including when you don't have the tool selected. This command can be useful when you are attempting to change the temperature of tools while they are not selected. The command `G10` allows you to change the temperature or offset of a specific tool.

`G10 Pnnn Xnnn Ynnn Znnn Rnnn Snnn` :

* `Pnnn` : Represents the tool number of the tool you are attempting to change the temperature or offset of.
* `Xnnn` , `Ynnn` and `Znnn` : Represent the X, Y and Z offset of the tool
* `Rnnn` : The tool's standby temperature. Or the temperature of the tool when it is not selected, but was previously active.
* `Snnn` : The tool's active temperature. Or the temperature of the tool when it is selected.

Example: `G10 P1 X10 Y0 Z0 R120 S230` , This will set the offset of tool 1 to 10mm in the positive X direction. It will also set the active temperature of the tool to 230C and the standby temperature of the tool to 120C.

The `G10` command is especially useful for mixing and switching prints.

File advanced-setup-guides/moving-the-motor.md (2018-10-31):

# Moving The Motor

## Manually Move Motors

Before you power on your motors, you can manually move the extruder head around the printer. 

Follow the steps below in order to start moving the printer:

Move the extruder head to the center of the printer by hand. This should not take a lot of effort to do as long as the motors are not powered. 

{% hint style="warning" %}
Do Not manually move any motors _**QUICKLY**_. You could damage your electronics.
{% endhint %}

Once you move the motors, the motors will be powered and resist any force acted on them.

Go to the _Machine Control_ tab of the Duet Web Console.

Machine Control Tab in Duet Web Console

Press _Home All_, this will home all the axes of the printer and ensure that the origin of the printer is located at the front-top-left corner of the 3D printer. 

After the homing process is complete, you can see that the position of the 3D printer is updated in the _Machine Status_ tab on the Duet Web Console.

Press the X-10 button in the _Head Movement_ window. 

This will move the extruder carriage of the printer 10mm in the negative X direction, this should be towards the left if you are facing the front of the printer. 

Now press the Y-10 button.

This will move the printer -10 mm in the Y-direction. If you are facing the front of the printer, this should send the extruder carriage towards you. 

You can also press the Z buttons, but remember that the bed is all the way down and resting on the limit switch after the homing process. 

You will have to move the bed in the negative Z direction in order to move it up. 

Press the Z-10 button in order to move the bed up 10 mm.

You can keep pressing the buttons to move the extruder carriage to become more familiar with the directions and coordinate system of the Promega.

## **Absolute vs. Relative**

A 3D printer movement allows for two different modes, absolute and relative. 

These two terms are also used frequently in machining and other engineering processes.

### Absolute

 Absolute describes a position or command with respect to the origin or zero position. 

{% hint style="info" %}
The Promega origin is located in the Top-Left-Front corner. 
{% endhint %}

Run this to enter Absolute mode.

```text
G90
```

 **For example:**

Tell the printer to move \(20,20,20\). 

```text
G1 X20 Y20 Z20
```

Absolute mode will send the printer to the point where X = 20 mm, Y = 20 mm and Z = 20 mm.

If you told it again to go to \(20,20,20\) it would just stay there. The Duet would say: I am already there!

### Relative

Relative describes the position of a 3D printer relative to the previous point the printer was located at. 

Run this to enter Relative mode.

```text
G91
```

 **For example:**

Tell the printer to move \(20,20,20\). 

```text
G1 X20 Y20 Z20
```

Relative mode will send the printer 20 mm in the X-direction, Y-direction and Z-direction relative to its previous position. 

 If you told the printer to move \(20,20,20\) again, the printer will move 20 mm in the X, Y and Z directions for the second time.

#### This is the difference between absolute and relative.

#### Your printer will go to two completely different places depending on if you are in relative or absolute mode.

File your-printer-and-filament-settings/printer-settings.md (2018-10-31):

# Printer Settings \(Default\)

## CoreXY Motion Settings

{% hint style="warning" %}
Because the printer uses a CoreXY Motion setup, X and Y motion settings _**Must Be Identical.**_
{% endhint %}

### Feedrate \(Speed\)

X Motion: 9000 mm/min

Y Motion: 9000 mm/min

Z Motion: 2300 mm/min

#### Input Code:

```text
M203 X# Y# Z#
```

### Acceleration

X Acceleration: 3000 mm/s^2

Y Acceleration: 3000 mm/s^2

Z Acceleration: 75 mm/s^2

#### Input Code:

```text
M201 X# Y# Z#
```

### Jerk

X Jerk: 350 mm/min

Y Jerk: 350 mm/min

Z Jerk: 50 mm/min

#### Input Code:

```text
M566 X# Y# Z#
```

## Compound Mixing: Extruder Motor Settings

{% hint style="info" %}
E parameter format: E \[ Left Motor Value \] : \[ Right Motor Value \]
{% endhint %}

### Feedrate \(Speed\)

Left Motor: 5000 mm/min

Right Motor: 5000 mm/min

#### Input Code:

```text
M203 E#:#
```

#### Example:

I want to set different rates between motors:

 Left motor feedrate \(speed\): 9000 mm/min 

Right motor feedrate \(speed\): 6000 mm/min

Input Code:

```text
M203 E#:#
```

### 

### Acceleration

Left Motor: 150 m/s^2

Right Motor: 150 m/s^2

#### Input Code:

```text
M201 E#:#
```

#### Example

I want to set different rates between motors:

 Left motor acceleration: 2000 mm/sec^2 

Right motor acceleration: 3000 mm/sec^2

Input Code:

```text
M201 E#:#
```

### Allowable Instantaneous Speed Change \(Jerk\)

Left Motor: 60 mm/min

Right Motor: 60 mm/min

#### Input Code:

```text
M566 E#:#
```

#### Example

I want to set different rates between motors:

 Left motor Jerk: 900 mm/min

Right motor Jerk: 600 mm/min

Input Code:

```text
M566 E#:#
```

## Single K'Tana: Extruder Motor Settings

{% hint style="info" %}
E parameter format: E \[ Left Motor Value \] : \[ Right Motor Value \]
{% endhint %}

### Feedrate \(Speed\)

Left Motor: 5000 mm/min

Right Motor: 5000 mm/min

#### Input Code:

```text
M203 E#:#
```

#### Example:

I want to set different rates between motors:

 Left motor feedrate \(speed\): 9000 mm/min 

Right motor feedrate \(speed\): 6000 mm/min

Input Code:

```text
M203 E#:#
```

### 

### Acceleration

Left Motor: 150 mm/s^2

Right Motor: 150 mm/s^2

#### Input Code:

```text
M201 E#:#
```

#### Example

I want to set different rates between motors:

 Left motor acceleration: 2000 mm/sec^2 

Right motor acceleration: 3000 mm/sec^2

Input Code:

```text
M201 E#:#
```

### Allowable Instantaneous Speed Change \(Jerk\)

Left Motor: 60 mm/min

Right Motor: 60 mm/min

#### Input Code:

```text
M566 E#:#
```

#### Example

I want to set different rates between motors:

 Left motor Jerk: 900 mm/min

Right motor Jerk: 600 mm/min

Input Code:

```text
M566 E#:#
```

## Bed Probe Settings:

### XY Offsets

X Offset: - 43.0

Y Offset: 25.0

#### Input Code:

```text
G31 T4 X-43 Y24
```

These values do not change. Do Not Change.

### Z Height Offset

This varies between each printer due to two reason:

1. The flatness of your bed directly affects the Z height offset. This will vary between each printer.
2. The absolute position of the bed probe \(as a whole\) can shift up and down, if not fixated.

#### Input Code:

```text
G31 Z#
```

## Z Limit Switch Settings:

### Height Value

This varies between each printer due to two reason:

1. The flatness of your bed directly affects the Z height offset. This will vary between each printer.
2. The absolute position of the Z Limit Switch can vary between printers.

#### Input Code:

Open up machine\_zendstop.g \(located under the sys folder\). Follow instructions inside the file.

```text
G92 Z#
```

## Temperature Settings

### PID Parameters

#### For Compound:

Proportional value \(Kp\): 22.1

Integral Value \(Ki\): 1.154

Derivative Value \(Kd\): 54.1

Maximum PWM: 1

#### For K'Tana:

Proportional value \(Kp\): 10.7

Integral Value \(Ki\): 0.477

Derivative Value \(Kd\): 38.8

Maximum PWM: 0.75

#### Input Code:

{% hint style="warning" %}
Changing these values can cause unexpected fluctuations in temperature. Proceed with caution.
{% endhint %}

For Compound Mixing:

```text
M301 H2 P# I# D# S1
```

For Left, Single K'Tana:

```text
M301 H1 P# I# D# S0.75
```

For Right, Single K'Tana:

```text
M301 H2 P# I# D# S0.75
```

### Maximum, Allowable Temperature

Maximum Temperature: 320 C

#### Input Code:

{% hint style="warning" %}
If changing this value, allow for a + 15 C buffer between your intended maximum, allowable temperature.
{% endhint %}

For Compound:

```text
M143 H2 S#
```

For Left, Single K'Tana:

```text
M143 H1 S#
```

For Right, Single K'Tana:

```text
M143 H2 S#
```

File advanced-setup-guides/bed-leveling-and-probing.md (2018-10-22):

# Bed Leveling & Probing

This page serves as an in depth guide to bed leveling. A good bed level will allow you to print a consistent first layer across the entire bed.

## Z-Probes

The Promega is equipped with two different Z-probes, an IR \(infra-red\) probe and a deployable endstop limitswitch. The default config.g file is set up to use the limit switch. This section covers the two different probes, their settings and how to use them. We recommend using the limit switch for less experienced users as it has proven to be more robust under many different circumstances.

### Probing Commands

* `G30`: Commands the printer to perform a single z-probe. The z-height of your printer will then be set to the Z-offset as defined in `G31`. Sending `G30 S-1` will cause the printer to perform a z-probe and print the trigger height but will not change the z-height of the printer, this can be used to find probe offset.
* `G31`: Sets the z-probe status and offset, this changes depending on which probe you wish to use.
* `M558`: Defines the z-probe type.
* `G29`: Executes bed leveling as defined by `M557`
* `M557 Pnnn Xmmm Ylll`: Defines the pattern that will be probed when `G29` is sent. `nnn` represents the point number if you wish to perform single point probing. A better option is to define a mesh with `Xnnn:mmm`, `Ylll:kkk` and `Sjjj`. Where `nnn` and `lll` are the minimum values for each axis and `mmm` and `kkk` are the maximum values. `jjj` represents the interval over the area you just defined. A working `M557` command for the Promega is: `M557 X50:370 Y10:350 S30`.
* `G32` will execute the _bed.g_ file located in _sys/_ on the microSD card.

### The Limit Switch Probe

> Warning: This limit switch is manually deployable. Remember to put the limit switch on the mount prior to probing, and remove the limit switch prior to printing or moving the bed to the nozzle.

**Mounting the Limit Switch Probe**

1. When mounted, the limit switch magnet should be firmly attached to the bottom of the mount as shown in the picture below.

   

2. Connect to the Duet Web Console. In the _Machine Status_ table observe the Z-probe cell. Press the Z-probe switch and you should see this value change from 0 to 1000. If this is not happening, it indicates a problem with the wiring of the limit switch. Stop and fix the wiring before continuing with this guide.
3. In order to unmount the limit switch simply remove it from its mount and stick it above the nozzle. Stick the limit switch against the metal mount so that the limit switch is pressed down. Now if you accidentally send the command `G30` with an unmounted z-probe, you will get an error: _"Error: Probe already triggered during move_" instead of a crash of the bed against the nozzle.

   

**Limit Switch Configuration Settings**

In the _config.g_ configuration file you can set certain properties of the Z-limit switch. The commands `M558` and `G31` are the most important here. If you wish to enable the limit switch as your z-probe you have to enter the following commands into your _config.g_ file:

```text
    M558 P4 I1 X0 Y0 Z1 H5 F100 T5000 ; Set Z probe type -- SET AS LIMIT SWITCH
    G31 P999 X40 Y-28.5 Z5.8 ; Set Z probe (limit switch) trigger value, offset
```

These two commands enable and configure the Duet board z-probe. Remember that you must comment all other M558 and G31 commands in order for these commands to take effect. If you enter these commands in the configuration file and then enter the same commands for the IR probe 10 lines below, the board will be configured to use the IR board.

The `M558` command above sets the Z-probe type.

* The `P4` parameter informs the firmware that the z-probe is a switch that is connected to the E0 endstop detection port. 
* `I1` inverts the reading on this port, the switch is wired as normally closed and therefore always outputs a value of 1000. 
* `X0 Y0 Z1` ensures that this limit switch is only used for homing the z-axis. Any non-zero value will enable homing on that axis. 
* `H5` sets the dive height of the probe. This defines the distance in mm that the probe will move after contact.
* `F100` is the feedrate of the homed axis. Reduce this value to slow down the bed more as it moves to make contact with the limit switch.
* `T5000` is the travel speed between probe points.

The G31 command sets certain z-probe settings such as offset and trigger height.

* `P999` sets the trigger value to 999. Whenever the z-probe trigger value is reached the board will register a detection. For the limit switch this value should not need to change.
* `X40 Y-28.5 Z5.8` Represents the offset of the z-probe to the nozzle, this value changes depending on which extruder you have mounted. If you have the K'Tana, the offsets of the z-probe to the nozzle are going to be different than the compound nozzle. It is also worth noting that the offset for the K'Tana nozzle is based on the right nozzle. The Z-offset to the z-limit switch varies per printer. We recommend that you tune your z-probe Z offset before printing. Follow the section below for calibrating the Z-offset of the limit switch.

**Calibrating the Limit Switch**

To find out the z-offset of the limit switch to the nozzle, follow the steps below. 1. Home the printer again, just to ensure you do not crash the printer throughout this process. 2. Print head to the center of the build plate by sending the command `G1 X187 Y154` 3. Heat up the bed to the preferred printing temperature. You can do this by sending the command `M140 Snnn` where `nnn` is your temperature in °C. You can always look up the recommended bed temperatures for specific materials online. For PLA, a bed temperature of 50°C will work well. For ABS-R, a bed temperature of 60°C is recommended. 4. Wait until the heated bed has reached temperature before continuing. 5. Set the Z-probe offset to 0 by entering the command `G31 G31 P999 X-40 Y28.5 Z0`. This will make it easier to gauge the distance between the Z-probe and the nozzle in the following steps. 6. Run the command `G29 S2`. This clears any active bed leveling compensation. This is **very** important as it will conflict with your updated Z-probe offset and induce a 0.1 - 0.3mm error depending on the magnitude of your bed leveling compensation at that point. 7. Deploy your Z-probe 8. Check whether the Z-probe is functioning correctly. This is a great step to perform before using your Z-probe in order to prevent crashes. Press your Z-probe limit switch and observe the change in value from 0 to 1000 in the Duet Web Console _Machine Status_ table in the _Z-Probe_ box. If the value does not change the Z-probe is wired or configured wrong, do not continue to the next step!

```text
![KWL6DTK3l4pAmrPv-zprobemachinestatus.png](../.gitbook/assets/gallery/2018-06-Jun/scaled-840-0/KWL6DTK3l4pAmrPv-zprobemachinestatus.png)
```

1. Move the bed towards the nozzle by sending the command `G1 Z20`. When you send the command `G30` the bed will move slowly and precisely to the Z-probe, if you send `G30` while the bed is at `Z100` or greater you will have to wait for a long time for the Z-probe to trigger.
2. Run the command `G30`. This will move the bed toward the z-probe until the limit switch triggers.
3. Now your Z0 is set to your Z-probe limit switches trigger height. This is because the Z-probe limit switch offset is 0mm. Now that we have set our Z0 to the trigger height we can move the bed toward the nozzle in order to find the distance between the trigger height of the Z-probe and the nozzle!
4. Retract the Z-probe.
5. Jog the bed up slowly toward the nozzle using the negative Z buttons in _Machine Control_ on the Duet Web Console. Read the next step!

   

6. As you are moving the bed up towards the nozzle you will encounter an axis limit. These axes limits are set for the X, Y and Z axes and will stop you from moving past a certain coordinate. This will make it harder to crash the printer. However, in this case we know what we are doing so we can disable the axes limits. Send the command `M564 S0` to disable the axis limits. To learn more about this command visit the [RepRap G-code wiki](https://reprap.org/wiki/G-code#M564:_Limit_axes).
7. **Be careful when moving the bed close to the nozzle. Use the 1mm and 0.1mm buttons.** Determining when the bed is touching the nozzle can be difficult. You might have to heat up the nozzle as you learned before in order to ensure that none of the filament from the hot-end gets in the way. Using a piece of paper to determine when the nozzle is touching the bed is also helpful. Grab a sticky-note or small piece of paper and place it under the nozzle. Then carefully jog the bed into the nozzle, move the paper back and forth. When you feel the nozzle grab the paper your nozzle is touching the bed!. 
8. Record the Z-value that the printer is currently displaying in _Machine Status_. The absolute \(non-negative\) of this value is your Z-probe offset. It might be a good idea to write down this value.
9. Enter the command `G31 P999 X-40 Y28.5 Znnn` where `nnn` is your Z-probe offset.
10. Move the bed away from the nozzle `G1 Z20`.
11. Deploy your Z-probe!
12. Send the command `G30`.
13. Move the bed back up to the nozzle as described in the steps above. Your Z value should be 0 when the bed is touching the nozzle. If it is not you might need to tune the Z-probe offset or repeat the process.
14. In order for these changes to take effect permenantly, you will have to open up your _config.g_ file and update the Z-offset of this command there. Follow the section below.

**Troubleshooting the Limitswitch**

### The IR Probe

The IR probe is located on the right side of the nozzle fan duct. The IR probe should be as parallel to the bed as possible. The IR probe functions by emitting Infra-Red rays \(hence the name IR probe\) at the bed and receiving them when they are reflected off a surface at a specific distance. Because not every surface is consistant, this detection height changes per surface. However, even variations within one surface can cause a difference in detection height. For example, glue from your previous print or a dirty print surface. This will all cause error and noise within your eventual bed level. We have found that this z-probe is very precise, but not always accurate. You will find that the limit switch is sometimes much better suited for some situations, such as a glass bed. While the IR probe is sufficient for others. For the best results we recommend a clean and dark surface such as a black print bed sheet. Follow the guide below for configuring your printer to use the IR probe.

**Configuring the IR Probe**

To use the IR probe a number of settings have to be changed in _config.g_. Ensure that the IR probe is parallel to the bed before using it. The following code should be entered or uncommented in _config.g_:

```text
    M558 P1 X0 Y0 Z1 H5 F120 T5000 ; Set Z probe type -- SET AS IR_PROBE
    G31 P450 X-30.4 Y-30.7 Z2.6 ; Set Z probe (IR) trigger value and offset
```

Remember that it is best practice to comment or remove all other instances of these commands in the configuration file, this will prevent you from mistakenly configuring and enabling the other z-probe. This code is for the compound nozzle, to obtain this code for the K'Tana nozzle visit the [M3D Promega GitHub Repository](https://github.com/PrintM3D/Promega).

The `M558` command above sets the z-probe type:

* `P1` sets the z-probe type.
* `X0 Y0 Z1` defines which axis this probe homes, any non-zero value enables that axis. In this case this probe only zeroes the z-axis.
* `H5` configures the dive height to 5mm. The dive height is the vertical distance the bed moves between probe moves
* `F120` sets the feedrate of the probe move.
* `T5000` sets the travel feedrate, the speed of travel in between probe moves.

The `G31` command sets the z-probe status:

* `P450` sets the trigger value, for the IR probe this **has** to be less than ~500 or the z-probe will not trigger. Manually test the z-probe trigger value before changing!
* `X-30.4 Y-30.7` defines the offset from the nozzle to the IR probe.
* `Z2.6` sets the z offset of the IR probe. This will have to be changed whenever you change the mounting height of the z-probe or whenever you change print bed material.

**Calibrating the IR Probe**

To discover the z-offset of the IR probe to the nozzle follow the steps below:

1. Home the printer and move to `X200 Y200 Z50`, probing in the center of the bed is the best idea as that is where the most printing occurs.
2. Heat up your bed and wait for it to reach temperature. Ensure that your print bed is clean. 3. Heat up your nozzle in order to remove any filament or debris on the nozzle tip.
3. Turn off bed leveling with `G29 S2`, bed leveling can interfere with probing the bed.

> Always disable bed leveling before probing or bed leveling, they will interfere with each other!!! &lt;

1. Check that the z-probe is functioning correctly by **manually** jogging the bed to the nozzle. You should see the Z-probe value in the Duet Web Console _Machine Status_ table change **before** the nozzle hits the bed. Remember the trigger value of the z-probe, this will vary per print surface.
2. Enter the command `G31 Pn Z1.0` where `n` is a value less than what you recorded in the previous step. The z-probe will trigger whenever it detects a value greater than `n`. `Z1.0` represents a stop gap to prevent a crash if you do send `G30`.
3. Jog the bed up until the bed is touching the nozzle, a piece of paper can help to determine when the nozzle is touching the bed. When the nozzle and bed are touching send command `G92 Z0`. This will set the current z-height of the printer to 0.
4. Move the bed to `Z20` with `G1 Z20`. 7. Send the command `G30 S-1` this will print out the z-height of the bed when the probe is triggered. It will **not** update your z-height value. Record the value that is printed out. To ensure that you are getting consistent values, you can repeat this step multiple times. Move the bed to `Z20` between every probe or you will get an error.
5. Send the `G31` command with your z-probe offset value set to the value you obtained in the step above. `G31 P450 X-30.4 Y-30.7 Znnn`, `nnn` is the value from the step above.
6. If you want these changes to affect your board permenantly, then copy and paste the command above into your _config.g_ file. Be sure to remove all other `G31` commands or comment them.
7. You have now successfully calibrated your IR probe. Send the command `G30` in order to probe the z axis. You can then move your bed up to your nozzle manually and verify that at `Z0` the nozzle is touching the bed.

## Bed Leveling

### Skipping the Bed

If you crash the bed into the nozzle it will cause the bed to skip and fall. After this happens your bed might no longer be level. Follow the steps below to skip a tooth on the bed in order to level it. Once the bed is level within ~3mm you can allow Mesh Bed Leveling to complete the rest.

1. Power cycle the printer and then turn it on. This will make it easier to manually move the motors.
2. Move the bed up to the nozzle. The best way to move the bed of the Promega is by holding the bed with both hands on either side in the center as shown below. If you want to stop your bed from falling down you can place a binder clip on the z-motor belt as pictured below.

   

   

3. Once the bed is at the nozzle, gauge the distance between the Z-slider and the top z-belt clamp as shown in the picture below. If one of these distances is greater than the other four it means your bed is not level. If you have a caliper you can measure the distance between the bed and each belt clamp corner.

   

   

4. Move the bed halfway down the printer. Hold the bed in place while gently pulling up on one corner. Keep pulling up until you hear a loud click and feel the bed move in that one corner.

   > Be careful with the amount of force you apply as you can break the belts or belt clamps.

5. Repeat step 3 in order to check that your bed is now level. If it is not skip another corner of the bed.

### Mesh Bed Leveling

1. Home the printer and heat up the bed to printing temperature. When the bed warms up it warps slightly. However, bed leveling compensation can compensate for this.
2. Define your mesh bed leveling grid with the `M557` command. The _config.g_ file should already have configured a working mesh: `M557 X50:370 Y10:350 S30`. You can change the maximum and minimum values of the mesh as well as the interval but be careful as running G29 with a wrong mesh can crash your printer. Be sure to take the offsets of the z-probe as defined in `G31` into account.
3. Disable any previous bed leveling compensation with the command `G29 S2` or `M561`, they accomplish the same goal. If you do not disable previous bed leveling you will find that your next heightmap will be off by around +- 0.3mm.
4. Ensure that you have properly configured your z-probe as in the sections above. Test your z-probe before probing by triggering the sensor and observing a change in the _Machine Status_ tab.
5. Make sure your bed is as level as possible. While bed leveling compensation can account for small variations in bed height it can't account for greater than 2-3mm.
6. If you are currently using the limit switch be sure to place it on its mount. If you are using the IR probe ensure that your bed is squeaky clean.
7. Send the command `G29 S0` to execute bed leveling immediately or `G32` which will execute _bed.g_. _bed.g_ can be a simpler option in the long run as it can automatically heat up your nozzle and bed and define your mesh grid before.
8. The bed leveling procedure will generate a _heightmap.csv_ file located in the _sys/_ folder. Once the bed leveling procedure completes it should display the heightmap. If this is not the case you can always go to _Settings &gt; System Editor_ and then click _heightmap.csv_ in order to see your heightmap.
9. Once bed leveling completes it should have already enabled the compensation. `G29 S1` enables compensation from _heightmap.csv_ by default and `G29 S2` disables compensation. In _config.g_ you should have the command `G29 S1` which enables bed compensation so you don't have to re-run the bed leveling procedure everytime.

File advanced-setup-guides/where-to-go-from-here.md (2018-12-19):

# Where To Go From Here

Now that you have completed the beginner guides you can continue to the following guides:

* Browse the [Getting Started]() chapter to ensure you know everything
* Read the [Updating SD Card Structure ]()guide to make sure your SD card is up-to-date.
* Read the [SD Card Structure](../documentation/software-firmware/sd-card-structure.md) guide to learn more about all the files on the SD card.

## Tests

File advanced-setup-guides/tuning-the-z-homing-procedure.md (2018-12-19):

# Tuning The Z Homing Procedure

{% hint style="warning" %}
CAUTION: This procedure involves heating the nozzle to high temperatures. Be very careful to not touch the nozzle or heater block, as they WILL BE HOT!
{% endhint %}

{% hint style="warning" %}
CAUTION: This procedure heats the print bed. Do not touch the bed as it WILL BE HOT!
{% endhint %}

## Tuning the Z-homing: Automated Procedure 

We offer an automated procedure for tuning the Z-homing in addition to a manual process. The automated procedure is preferred \(continue reading just below\), although if your printer encounters any issues during this process, the manual procedure steps at [Tuning the Z-homing: Manual Procedure](tuning-the-z-homing-procedure.md#tuning-the-z-homing-manual-procedure) may help you troubleshoot the particular error.

{% hint style="info" %}
A Thank You! goes out to our Promega community for developing these macros.
{% endhint %}

**The relative distance between the bed and the nozzle depends on your Promega configuration \(K'tana vs. Compound, glass vs. no glass, etc.\)** Ideally whenever you home the printer and send the command `G1 X0 Y0 Z0` \(telling the printer to go to \(0,0,0\)\) the print bed will touch the nozzle. However, as outlined above, the relative distance between the bed and the nozzle varies depending on your setup. Follow the steps below to update the Z configuration of your printer.

#### This procedure consists of four broad steps:

* Step 1: Prerequisites are covered
* Step 2: We calibrate the Z probe's location relative to the nozzle.
* Step 3: We calibrate the full Z travel of the printer \(which depends on bed glass, nozzle installation, etc.\)
* Step 4: We perform a mesh bed leveling.

### Step 1: Prerequisites

#### Verify your printer configuration is up to date before completing this procedure. 

In particular, make sure the **configuration files**:

```text
machine_axisdimension.g
machine_zendstop.g
machine_zprobe.g 
```

are present on the SD card.

Along with the **macros**:

```text
_1_Calibrate_Z_Probe.g
_2_Set_Z_Endstop_Height.g
_3_Mesh_Bed.g. 
```

Let's verify. Go the web interface, 

1. Choose _Settings. T_hen _System Editor_. 
2. Scroll down.
3. Ensure the three **configuration files** are present. 

Next, 

1. Choose _Macros_, 
2. Look for a folder named _Printer Setup_
3. Ensure the three **macros files** are contained within. 

If any of these files are missing, review the instructions at [Updating SD Card Structure]() to update your printer, then return to this page to tune the Z-homing procedure.

### Step 2: Z Probe Location Calibration

#### First, we will teach our printer the vertical distance between the nozzle and the deployed Z probe. 

{% hint style="info" %}
The Z probe should initially be stowed. If the probe is deployed, please retract it now. 
{% endhint %}

Begin by running the _\_1\_Calibrate\_Z\_Probe.g_ macro: 

1. Choose the _Macros_ tab in Duet Web Control
2. Enter the _Printer Setup_ folder
3. Click the _\_1\_Calibrate\_Z\_Probe.g_ file entry. 
4. Confirm you want to run the macro. Follow the onscreen prompts. 

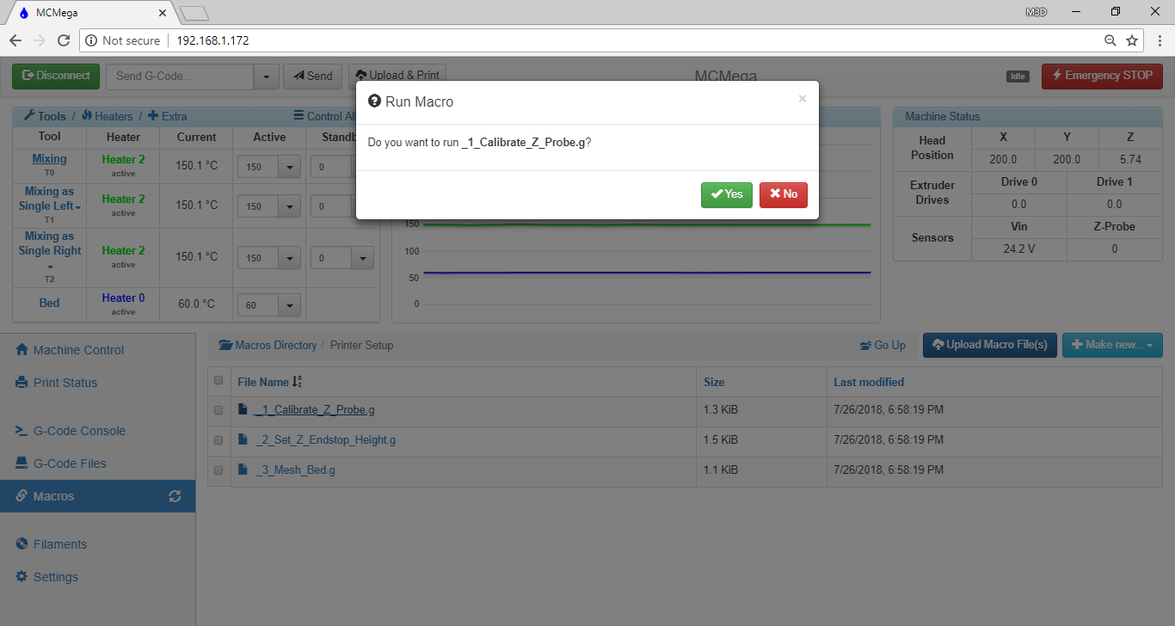
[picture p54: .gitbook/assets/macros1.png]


{% hint style="info" %}
At times, the visual prompts may disappear while the printer continues to operate. This is normal, and you should wait for the next dialog requiring user input.
{% endhint %}

After homing, heating, and bringing the bed within ~20 mm of the nozzle, the macro will ask for your input to move the bed so that it just makes contact with the nozzle. 

Make sure your Z probe is stowed, then use the \(-\) buttons to move the bed closer to the nozzle. 

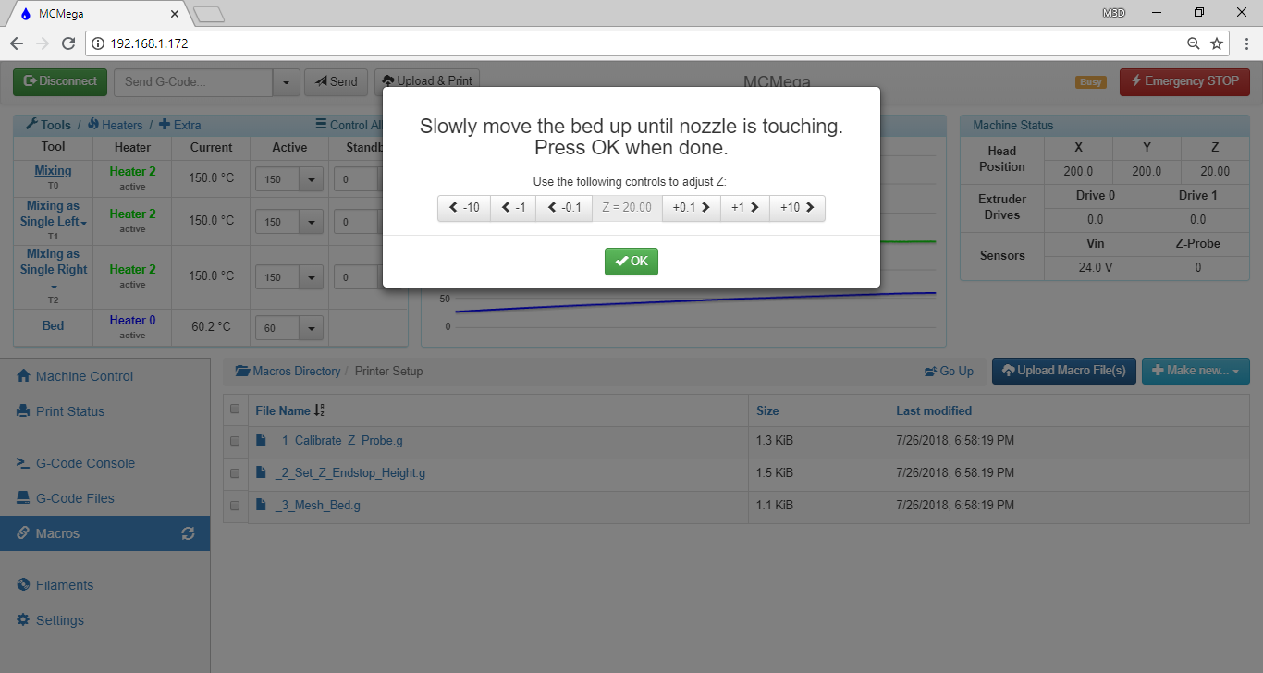
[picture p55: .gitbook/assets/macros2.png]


A post-it note or similar sheet of paper can be a useful tool to check the distance between the bed and nozzle, but always be careful to avoid touching the hot nozzle or heater block. 

The post-it will slide relatively easily until there is a 0.1 mm gap between the bed and nozzle. 

* If you step the bed closer to the nozzle in 0.1 mm increments, you can use the post-it note as a feeler gauge. 
* When you feel resistance to the motion of the post-it, remove it from the gap between the nozzle and bed. If the post-it slides out from between the two without much resistance, we recommend moving 0.1 mm closer \(again, use \(-\) buttons\). 

{% hint style="info" %}
This dialog will show a Z= value, but it is not important at this point to make note of that value. 
{% endhint %}

Once the bed and nozzle are touching, choose _OK_.

Deploy the Z probe when asked. 

Then, continue stepping through the automated process, following the on-screen prompts. 

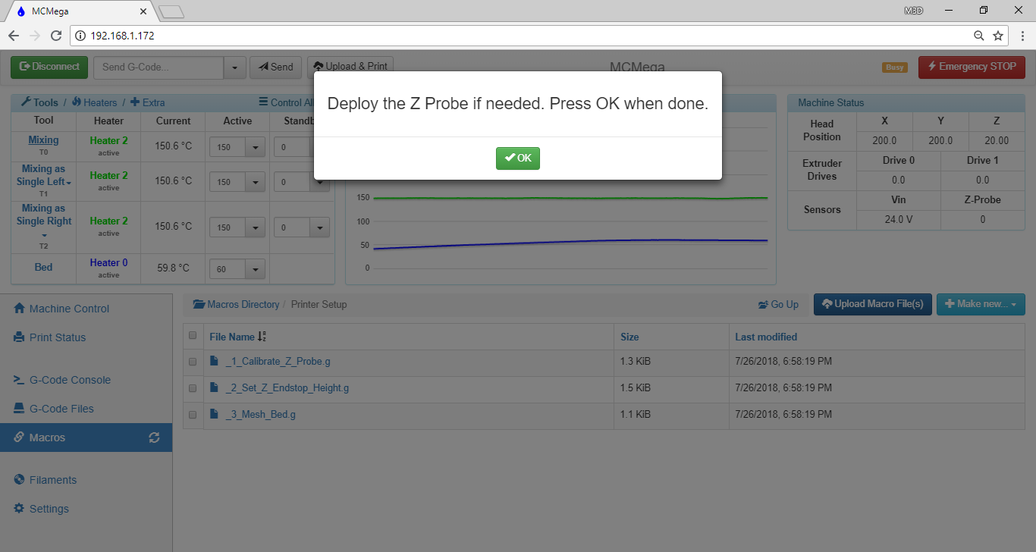
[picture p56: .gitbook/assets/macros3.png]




The printer will raise the bed until it just makes contact with the deployed probe, at which point the Z value in the _Machine Status_ display is a measure of the distance between the nozzle and the height at which the probe triggers. **The next step will have you place this value in your machine configuration files so that the printer powers on with the proper Z calibration routines in the future.**

Follow the on-screen prompts, making note of the Z value in the _Machine Status_ area of the Duet Web Control page. 

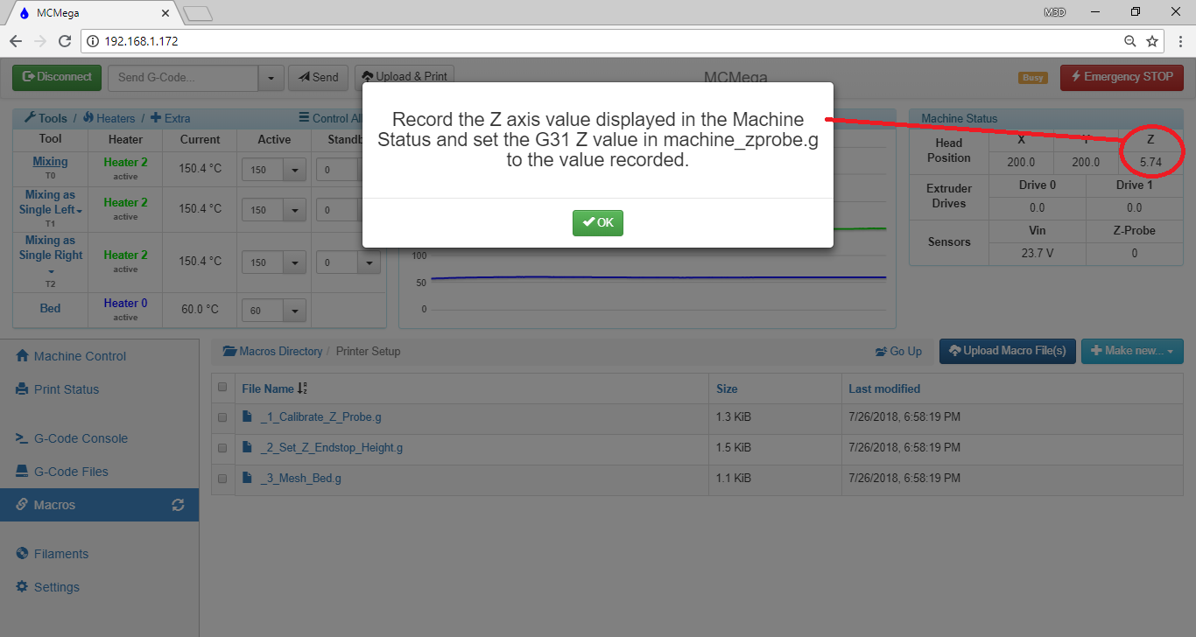
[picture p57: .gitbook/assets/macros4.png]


In the example shown, the bed triggered the Z probe at a height of 5.74 mm. 

We will now transfer this value to the configuration file _machine\_zprobe.g_. 

After viewing the remaining prompts

1. Choose the _Settings_ tab. Then _System Editor._
2. Scroll down to the _machine\_zprobe.g_ file. 
3. Click on the filename to open the file for editing.

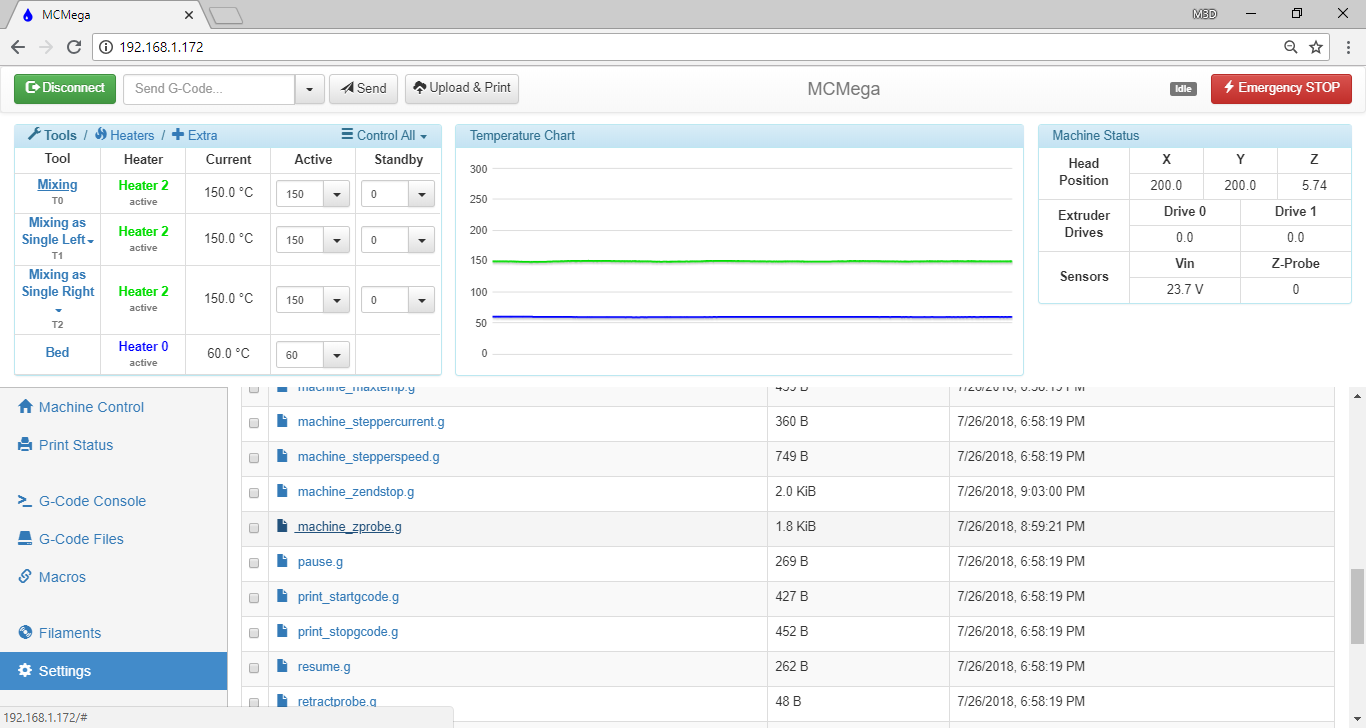
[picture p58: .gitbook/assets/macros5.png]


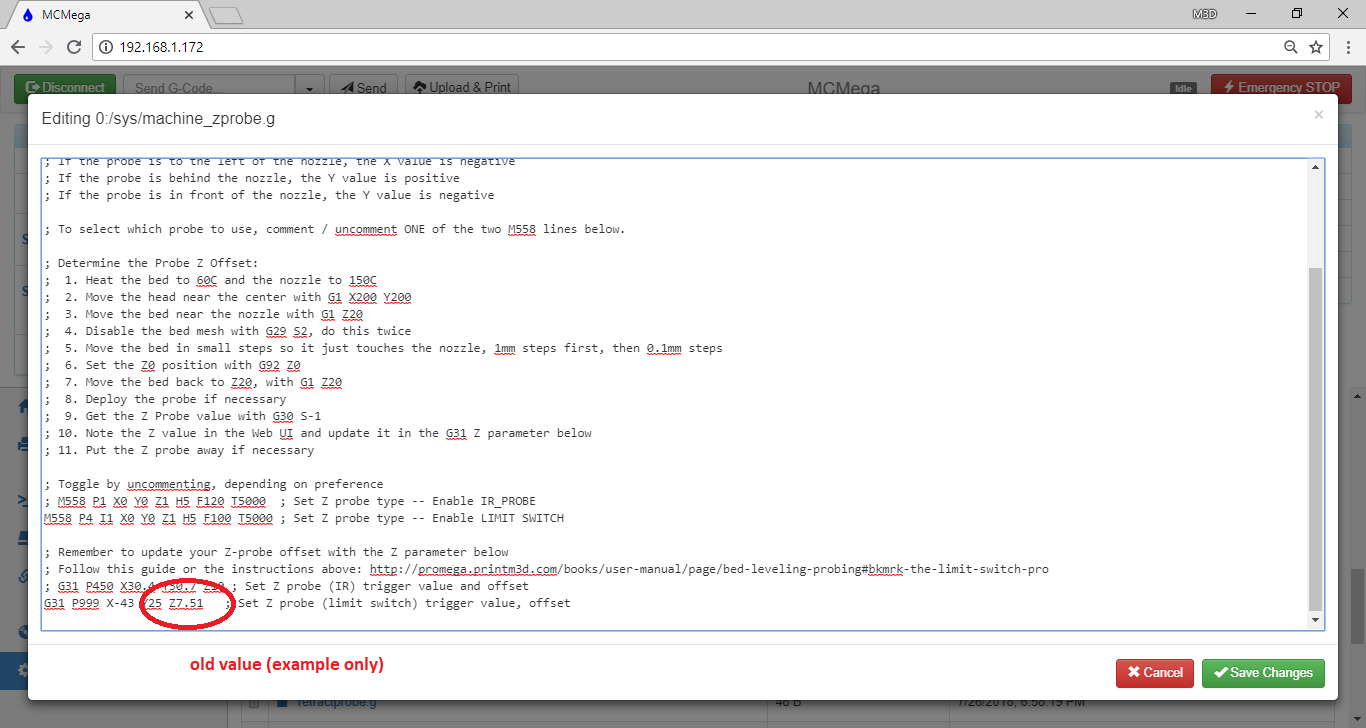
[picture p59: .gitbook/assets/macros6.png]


Near the very bottom of the file, you will see a line that begins "G31" that we will update with our new Z offset value. In the image above, you can see our printer had an old Z value of 7.51 mm.

Update the Z value by changing just the numeric part to the value from the _Machine Status_ area of Duet Web Control. In our example, "Z7.51" changes to "Z5.74". 

{% hint style="info" %}
There is no space between the letter 'Z' and the numeric value. 
{% endhint %}

Choose _Save Changes_ after you have updated the value.

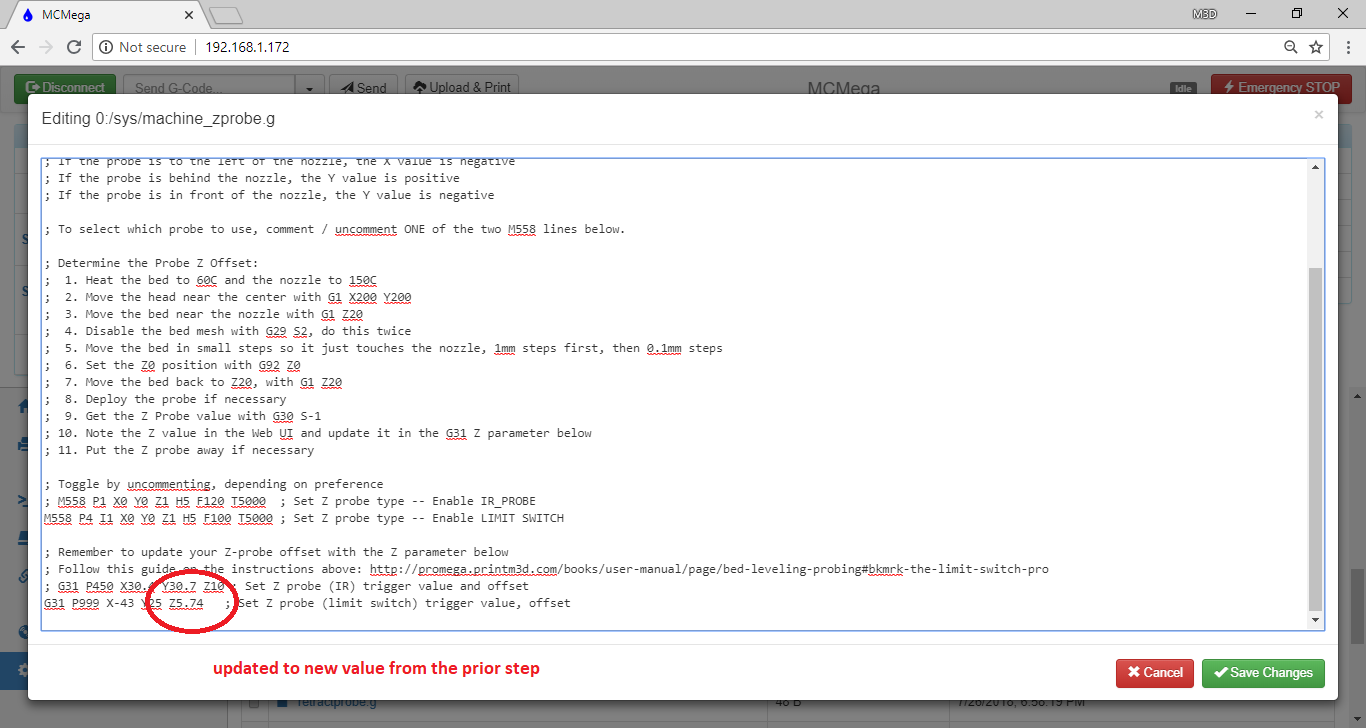
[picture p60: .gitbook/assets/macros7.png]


### Step 3: Full Z Travel Calibration

Next, we will teach our printer the precise distance the bed travels from the bottom of the printer, when it has just made contact with the Z maximum endstop, to the top of the printer \(Z=0\) where prints begin. **The Z probe should be stowed. If the probe is deployed, please retract it now.** 

Run _**\_2\_Set\_Z\_Endstop\_Height.g**_: 

1. Choose the _Macros_ tab in Duet Web Control. Enter the _Printer Setup_ folder.
2. Click the _\_2\_Set\_Z\_Endstop\_Height.g_ file. 

When asked to confirm running the macro, choose _Yes._

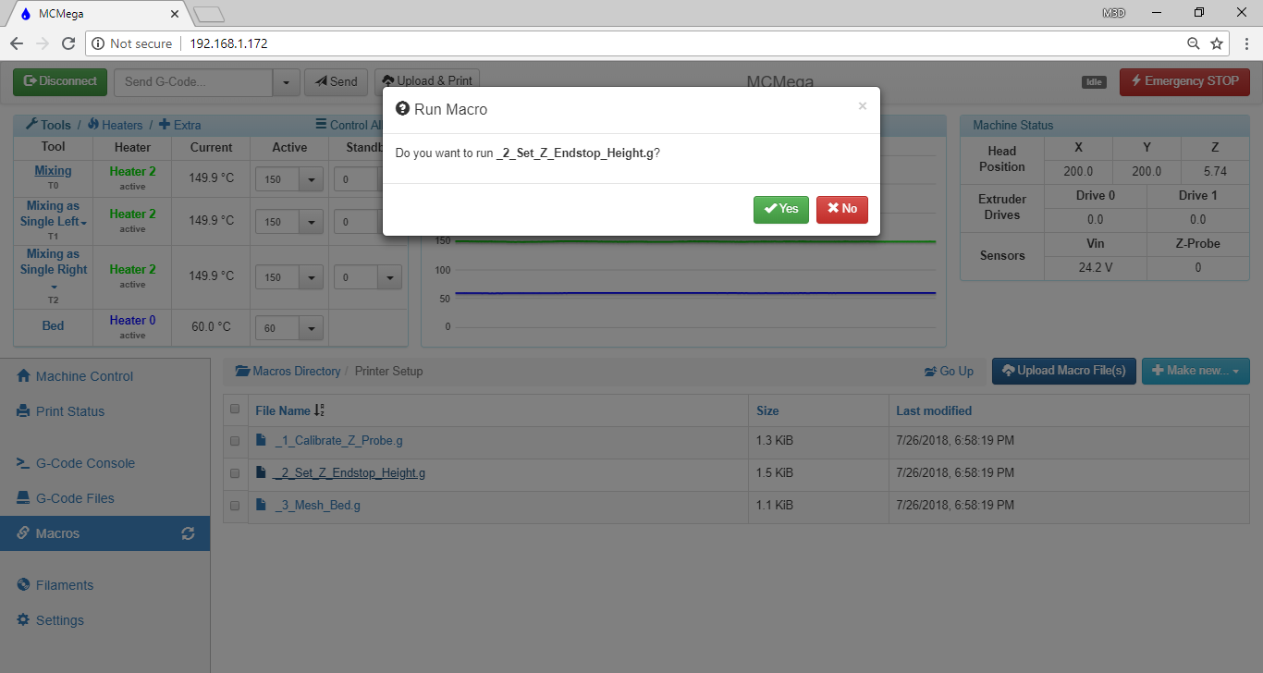
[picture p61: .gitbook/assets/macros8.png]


At times, the visual prompts may disappear while the printer continues to operate. This is normal, and you should wait for the next dialog requiring user input.

After homing, heating and bringing the bed within ~20 mm of the nozzle, the macro will ask for your input to move the bed so that it just makes contact with the nozzle. 

Make sure your Z probe is stowed, then use the \(-\) buttons to move the bed closer to the nozzle.

We have measured the adjustment necessary to the current configuration value for Z maximum extent. **The next step will have you place this value in your machine configuration files so that the printer powers on with the proper Z calibration routines in the future.**

Follow the on-screen prompts, making note of the Z value in the _Machine Status_ area of the Duet Web Control page.

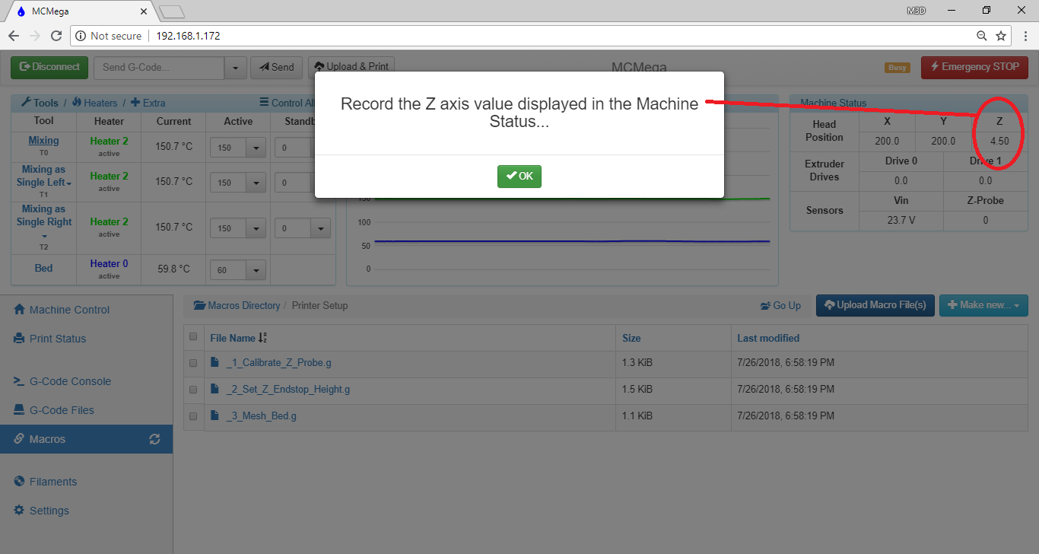
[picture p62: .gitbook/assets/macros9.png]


In the example shown, the bed made contact with the nozzle at a height the printer believes to be 4.5 mm. We need this contact to occur at a height the printer believes is actually 0 mm, meaning the Z extent programmed in the printer is currently 4.5 mm too large.

We will use the value from the previous step to update the configuration files _machine\_zendstop.g_ and _machine\_axisdimension.g_. 

After viewing the remaining prompts:

1. Choose the _Settings_ tab. Then _System Editor._
2. Scroll down to the _machine\_zendstop.g_ file. 
3. Click on the filename to open the file for editing.

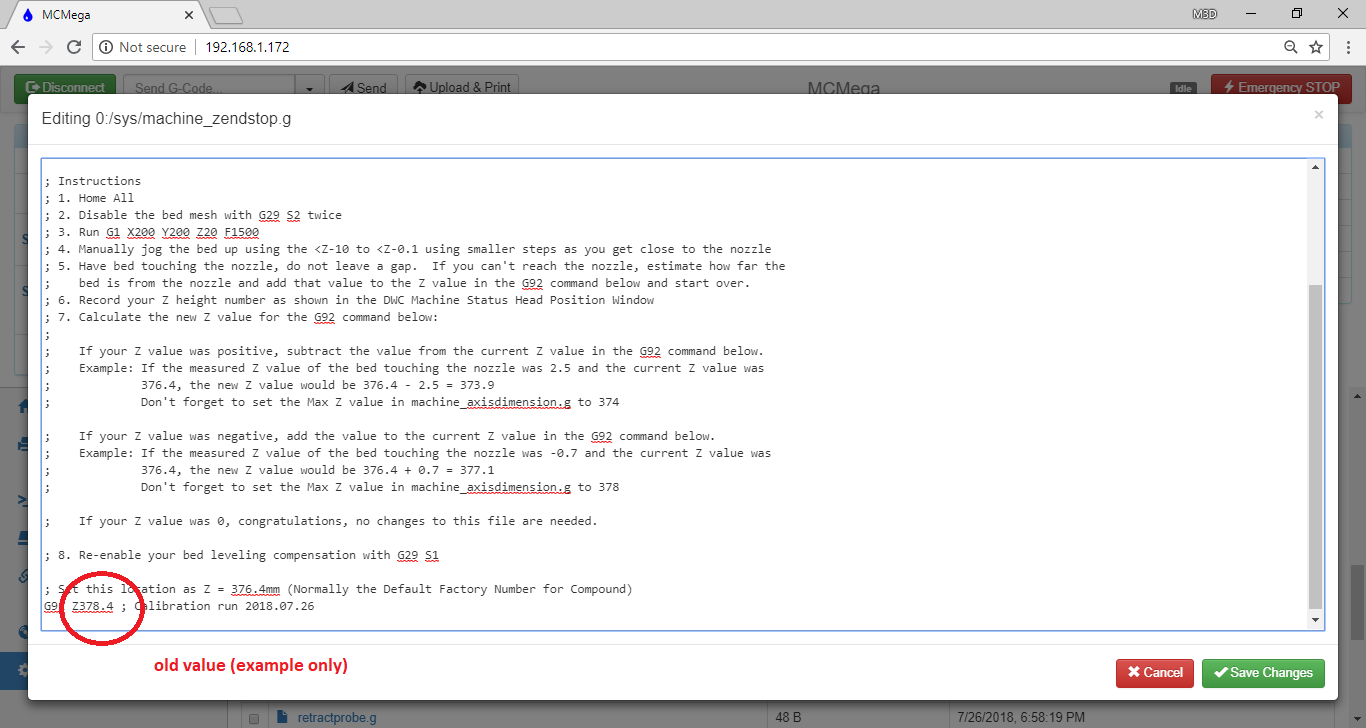
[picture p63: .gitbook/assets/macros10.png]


Near the very bottom of the file, you will see a line that begins "G92" that we will update with our new achievable Z value. In the image above, you can see our printer had an old Z value of 378.4 mm. We need to update this with a value calculated as: 

$$
new value = old value - step8valuenewvalue=oldvalue−step8value
$$

For example: 

> If the _machine\_zendstop.g_ file currently contains the command `G92 Z378.4` and I obtained a value of 4.5 mm, my new value would be 373.9 mm. 
>
> I would replace the current Z value in the G92 command so that the line reads `G92 Z373.9`

Choose _Save Changes_ after you have updated the value.



The values in _machine\_axisdimension.g_ implement safety and convenience features to avoid damage to the machine when everything is in working order and properly homed, and also need to be updated based on the result of step 8. These values prevent your bed, for example, from attempting to travel a large distance beyond the physical extent of your printer \(sometimes known as "crashing"\). 

1. Choose the _Settings_ tab. Then _System Editor._
2. Scroll down to the _machine\_axisdimension.g_ file. 
3. Click on the filename to open the file for editing.



Near the very bottom of the file, you will see a line that begins "M208 S0" that we will update with our new practical Z range. In the image above, you can see our printer had an old Z value of 379 mm. 

We will update the Z extent value contained in _machine\_axisdimension.g_ to reflect the achievable Z travel from step 8. 

In practice, we do the following: 

* Take the value just set in _config\_zendstop.g_, round to the next largest whole number, and set this value in _machine\_axisdimension.g_. 

For example: 

> We just set our Z value for the G92 command in _machine\_zendstop.g_ to 373.9. We will therefore set the Z value in _machine\_axisdimension.g_ to 374.



Choose _Save Changes_ after you have updated the value.

For best results, we recommend repeating step 8. In a properly calibrated printer, the resulting value of that process should be a Z of 0 mm. If the value is not 0 mm, repeat step 9 using the attained value.

### Step 4: Mesh Bed Leveling

Finally, we perform a multi-point bed probe to allow the printer to correct for small variances in the level and flatness of the bed. Run _\_3\_Mesh\_Bed.g_: choose the _Macros_ tab in Duet Web Control, enter the _Printer Setup_ folder, and click _\_3\_Mesh\_Bed.g_. When asked to confirm running the macro, choose _Yes_. 



This macro takes several minutes to run. Once completed, you will see a graphical view of the probing results.



These results are automatically saved and ready for use during this printing session and each time you power on the printer, so you have completed tuning your Z homing and no further action is necessary at this time. If you'd like to learn more about mesh bed compensation, however, you can read more at [Bed Leveling & Probing](https://promega.printm3d.com/~/edit/drafts/-LOsd42LlDMsCQgG4bzO/firmware-guides/bed-leveling-and-probing).

## Tuning the Z-homing: Manual Procedure 

**If you have already successfully run the procedure at** [**Tuning the Z-homing: Automated Procedure**](tuning-the-z-homing-procedure.md#tuning-the-z-homing-automated-procedure)**, you can ignore this section. The automated process is the preferred procedure. This manual procedure is meant to accomplish the same end result, but allows for additional diagnostics during the process, should they be required.**

Currently, this procedure is equivalent to steps 6 through 10 of the automated procedure above. The calibration of Z probe relative to nozzle and running of the mesh bed level are not covered here.

**The relative distance between the bed and the nozzle depends on your Promega configuration \(K'tana vs. Compound, glass vs. no glass, etc.\) The macro** _**machine\_zendstop.g**_ **allows for Z0 to line up properly. We recommend tuning this macro once after receiving your printer, as well as following any configuration changes to the printer \(such as extruder style or print surface change\).**

Ideally whenever you home the printer and send the command `G1 X0 Y0 Z0` \(telling the printer to go to \(0,0,0\)\) the print bed will touch the nozzle. However, as outlined above, the relative distance between the bed and the nozzle varies depending on your setup. Follow the steps below to update your _machine\_zendstop.g_ file.

1. Verify your printer configuration is up to date before completing this procedure. In particular, make sure the file _machine\_zendstop.g_ is present on the SD card. To verify: in the web interface, choose _Settings_ and then _System Editor_. Scroll down and ensure _machine\_zendstop.g_ is present. If it is not, first review the instructions at [Updating SD Card Structure]() to update your printer, then return to this page to tune the Z-homing procedure.
2. Home the printer if you have not already done so \(see [Homing the Printer](../beginners-setup-guides/homing-the-printer.md)\).
3. Send the command `G29 S2` to disable bed leveling. Bed leveling can conflict with your homing value.
4. Move the printer to a height of Z = +10 mm with the command `G1 Z10`
5. Move the print head toward the center with `G1 X200 Y200`
6. Jog the bed up the nozzle with the buttons in machine control until the bed is touching the nozzle. Use the _Z1mm_ and _Z0.1mm_ buttons. Remember that you are about 10mm away from the nozzle.

   

7. Once the bed is properly touching the nozzle record the Z-value in _Machine Status_ on the Duet Web Console_._ This value will be used in the next step.
8. Open the _machine\_zendstop.g_ file in the _Settings_ tab of Duet Web Control. This file is called during the homing process of the Z-axis. Find the `G92` command at the end of the file. This command sets the z-axis height when the bed is moved completely away from the nozzle \(that is, it is at the bottom of the printer and has triggered the Z maximum endstop\).
9. Update this value with the following formula: new value = old value - step6valuenewvalue=oldvalue−step6value For example: if the _machine\_zendstop.g_ file currently contains the command `G92 Z376.4` and I obtained a value of -0.6, my new value would be 377mm. I would remove the current G92 command from the _machine\_zendstop.g_ file and replace it with`G92 Z377`
10. Save the file and home the printer again. Although you should now be able to enter the command `G1 Z0` , I don't recommend it. Manually jog your bed to the nozzle again to ensure that Z0 is when the bed is touching the nozzle.

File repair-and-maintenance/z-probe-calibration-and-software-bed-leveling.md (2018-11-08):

# Z-Probe Calibration & Software Bed Leveling

This guide will walk you through setting the Z-offset of a Z-probe sensor. This is necessary in order to allow you to probe the bed accurately. 

The Promega comes equipped with two different Z-probes:

* The Limit Switch 
* The IR Probe. 

{% hint style="info" %}
This guide can be followed to configure either one. 
{% endhint %}

Whenever you home the printer, the current Z-value of the printer is set based on the limit switch on the bottom of the printer. Whenever you "probe" the bed, meaning you touch the bed against the limit switch probe on the extruder or the IR probe on the extruder, the Z-value will now be based on that probe move. However, in order to do this accurately, you will have to configure the distance between the nozzle and the trigger height of the Z-probe. This is because the firmware will set the Z-value of the printer to the Z-probe offset, as configured in this guide, whenever the Z-probe is triggered during a probe move.

## Calibrating the Limit Switch

To find out the z-offset of the limit switch to the nozzle, follow the steps below.

Home the printer again, just to ensure you do not stall the printer throughout this process. 

Print head to the center of the build plate by sending the command

```text
G1 X187 Y154
```

Heat up the bed to the preferred printing temperature. You can do this by sending the command `M140 Snnn` where `nnn` is your temperature in °C. You can always look up the recommended bed temperatures for specific materials online. 

{% hint style="info" %}
For PLA, a bed temperature of 50°C is recommended. 

For ABS-R, a bed temperature of 60°C is recommended. 
{% endhint %}

Wait until the heated bed has reached temperature before continuing. 

Set the Z-probe offset to 0 by entering the command:

```text
G31 P999 X-40 Y28.5 Z0
```

This will make it easier to gauge the distance between the Z-probe and the nozzle in the following steps. 

Run the command:

```text
G29 S2
```

This clears any active bed leveling compensation. This is **very** important as it will conflict with your updated Z-probe offset. 

{% hint style="warning" %}
It will induce a 0.1 - 0.3 mm error.
{% endhint %}

Deploy your Z-probe!



Check whether the Z-probe is functioning correctly. 

{% hint style="info" %}
This is a great step to perform before using your Z-probe in order to prevent crashes. 
{% endhint %}

Press your Z-probe limit switch and observe the change in value from 0 to 1000 in the Duet Web Console _Machine Status_ table in the _Z-Probe_ box. 

{% hint style="warning" %}
If the value does not change the Z-probe is wired or configured wrong, Do Not continue to the next step!
{% endhint %}

Z Probe Is Not Triggered

Move the bed towards the nozzle by sending the command `G1 Z20`. When you send the command `G30` the bed will move slowly and precisely to the Z-probe, if you send `G30` while the bed is at `Z100` or greater you will have to wait for a long time for the Z-probe to trigger.

Run the command `G30`. This will move the bed toward the z-probe until the limit switch triggers.

Now your Z0 is set to your Z-probe limit switches trigger height. This means that if you go to Z0 with the command `G1 Z0` it will send the bed to the trigger height of the limit switch. This is because the Z-probe limit switch offset is 0mm, and the firmware sets the Z-height of the printer to the Z-probe offset whenever the probe is triggered during the probe move.

Now that we have set our Z0 to the trigger height we can move the bed toward the nozzle in order to find the distance between the trigger height of the Z-probe and the nozzle!

Retract the Z-probe.

Jog the bed up slowly toward the nozzle using the negative Z buttons in _Machine Control_ on the Duet Web Console. Read the next step!



As you are moving the bed up towards the nozzle you will encounter an axis limit. These axes limits are set for the X, Y and Z axes and will stop you from moving past a certain coordinate. This will make it harder to stall the printer. However, in this case we know what we are doing so we can disable the axes limits. Send the command `M564 S0` to disable the axis limits. To learn more about this command visit the [RepRap G-code wiki](https://reprap.org/wiki/G-code#M564:_Limit_axes).

**Be careful when moving the bed close to the nozzle. Use the 0.1mm buttons.** Determining when the bed is touching the nozzle can be difficult. Heat up the nozzle as you learned before in order to ensure that none of the filament from the hot-end gets in the way. Using a piece of paper to determine when the nozzle is touching the bed is also helpful. Grab a sticky-note or small piece of paper and place it under the nozzle. Then carefully jog the bed into the nozzle, move the paper back and forth. When you feel the nozzle grab the paper your nozzle is touching the bed!. 

Record the Z-value that the printer is currently displaying in _Machine Status_. The absolute \(non-negative\) of this value is your Z-probe offset. It might be a good idea to write down this value.

Enter the command `G31 P999 X-40 Y28.5 Znnn` where `nnn` is your Z-probe offset.

Enter the command `M564 S1` in order to re-enable your axes limits.

Move the bed away from the nozzle `G1 Z20`.

Deploy your Z-probe!



Send the command `G30`.

Retract your Z-probe!

Move the bed back up to the nozzle as described in the steps above. Your Z value should be 0 when the bed is touching the nozzle. If it is not you might need to tune the Z-probe offset or repeat the process.

In order for these changes to take effect permanently, you will have to open up your _config.g_ file and update the Z-offset of this command there. If you have the newer version of the SD card, you will have to find _machine\_zprobe.g_ and open that instead.

Find the un-commented `G31` command and change the `Z` parameter value to the value you just found.

Save the file, now if you reboot your Duet the Z-probe offset will be saved. If you ever make a mechanical change to the printer, skip the bed and so on, you will have to recalibrate your Z-probe following the steps above.

## Automatic Bed Leveling Compensation

To accommodate for small discrepancies in the bed level of the Promega, you can enable bed leveling with `G29` , however, this command will require a _heightmap.csv_ file. Each _heightmap.csv_ file will be unique to your Promega, and sometime even unique to a specific time. If you stall your printer or otherwise misalign your bed, you will have to re-run mesh bed leveling. Bed leveling compensation can compensate for about 2mm of error. If your error is greater, follow the [mechanical leveling guide](mechanical-bed-leveling.md) via skipping. Follow the steps below to generate a _heightmap.csv_ file and enable bed leveling compensation.

Home the printer if you have not already done so.

Heat up the print bed to your preferred printing temperature. The Promega's bed will warp differently depending on what temperature it is heated up to.

Wait until the bed has reached its temperature before continuing. This could take a few minutes.

Deploy the Z-probe.

Send the command `G1 X200 Y200 Z20` followed by the command `G30`.

Send the command `G32` , this will start the mesh bed leveling process. The mesh is defined in the configuration files on the SD card, and should not need to be changed.

Wait for the mesh probing to complete. This could take a while as it probes over 100 points on the bed.

Once the leveling completes, it will generate the _heightmap.csv_ file in the _sys/_ folder on the microSD card. It will also display the heightmap on the Duet Web Console. This is a great tool to observe and visualize any error in the levelness of your bed. Remember that this graph is inflated **massively** and represents a 400mm by 400mm area**.** A height difference of  ± 1mm between the corners of the print bed is expected. Below you can see heightmaps. The one on the left is a normal heightmap, the one on the right is a good heightmap \(courtesy of @talrynn\(John\) on discord\). With mesh bed leveling compensation, there should be no difference in print quality or ability.  



Bed leveling compensation will be automatically enabled once bed leveling completes. It is important to **remember to disable bed leveling compensation whenever you are finding constants and offsets on the Z axis**. Otherwise the bed leveling compensation will conflict with the offset you obtain. If you want to disable bed leveling compensation send the command `G29 S2` , to enable bed leveling compensation after disabling it, send the command `G29 S1`

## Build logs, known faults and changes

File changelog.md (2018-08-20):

# Changelog

## **1.19: Inception - June 26, 2018**

* Updated Printed Parts:
  * 051402\_C1 Z Top Belt Clamp
  * 051404\_B3 Z Bottom Belt Clamp
  * 051168\_B2 Y Limit Switch Holder
  * 051166\_C1 X Limit Switch Holder
  * 051112\_B1 Spool Holder

## **1.20: June 26, 2018**

* New Z Belt Tightening method:
  * Clamping with a washer
* Updated Printed Parts:
  * Z Belt Bottoms: REMOVED
  * 051224\_A2 Bed Terminal Cover
  * 051172\_B2 Bed \_ Power Switch Holder
  * 051108\_C1 Rear Cable Harness\_Base
  * 051134\_A2 Rear Cable Harness Support

## **1.21: July 13, 2018**

* Updated Printed Parts:
* Updated SD card contents.
* Updated wire connections \(board side\)
* Updated Printed Parts:
  * 051224\_A3 Bed Terminal Cover
  * 051108\_D1 Rear Cable Harness\_Base
  * 058302\_B1 Front Cable Harness Base
  * 058304\_A1 Front Cable Harness Cover

## **1.23: July 17, 2018**

* Updated Printed Parts:
  * 051162\_B2 Z Limit Switch Holder
  * 051404\_A1 Magnet Holder Left
  * 051405\_A1 Magnet Holder Right

## **1.24: July 23, 2018**

* Update Printed Parts:
  * 051176\_A2 Bed Limit Slider
  * 051174\_A2 Bed Limit Housing
* Bed Switch Endstop Improvements:
  * Reinforced soldering
  * Longer wire

## **1.25 : July 30, 2018**

* New public 3D printed part file names.
  * Naming conversion details under:
    * \Public\Printed Part Bin\Conversion Details\Naming Conversion - Details \(as of 7/27/201811\_37a.m.\).pdf
  * A copy of the entire bin before conversion is under:
    * \Public\Printed Part Bin\Conversion Details\Bin \(Prior To Naming Conversion\)
* Updated Printed Parts:
  * 058302\_B3 Front Cable Harness Base
  * 058302\_B3 Front Cable Harness Base\_Text
  * 058304\_A3 Front Cable Harness Cover
* Duet3D Hardware Update:

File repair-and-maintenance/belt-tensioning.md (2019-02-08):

# Belt Tensioning

As the Promega is used over time it is possible slack develops in the CoreXY or Z-assembly belts. This can be fixed easily by following the guides below. Properly tensioning your belts will address problems with backlash and XY skipping.

## CoreXY Tuning

In order to tension the CoreXY loosen the three screws as indicated below.

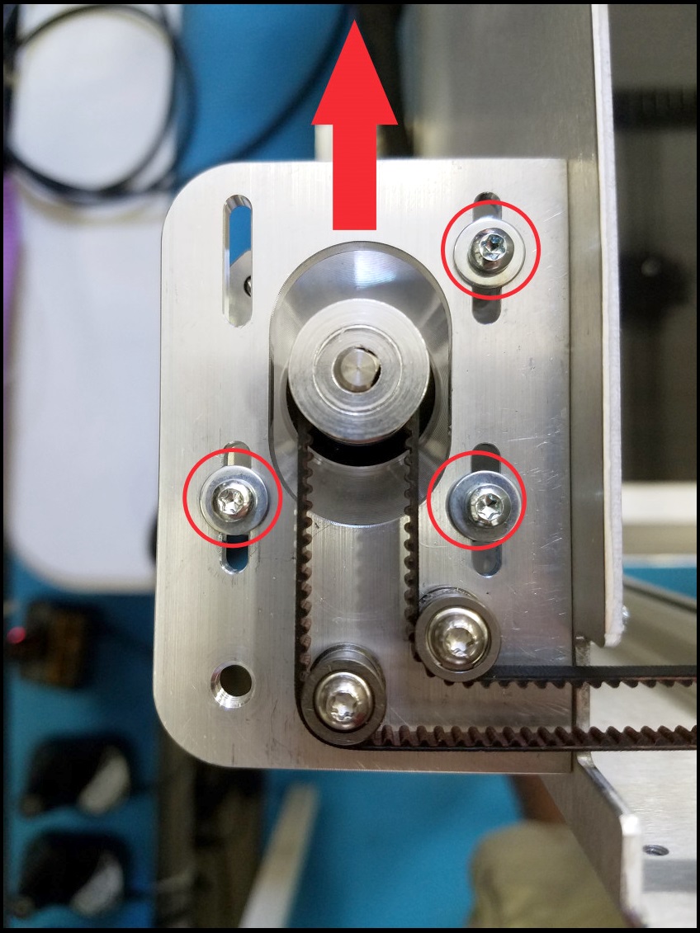
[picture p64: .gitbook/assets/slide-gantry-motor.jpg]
Tensioning the CoreXY Belts.


Once the screws are loosened you should be able to pull the motor to tension the belts. Pull in the direction of the arrow.

{% hint style="info" %}
You will **not** need to pull very hard to tension these belts, around 2 lb of force is sufficient.
{% endhint %}

Strum the belts near the extruder assembly to get an idea of the tension applied to the system by pulling the motor. Once you are satisfied with the tension, tighten the M3 screws back down.

Apply this same process to the other CoreXY motor.

{% hint style="warning" %}
Be sure to tension this belt system with the _**same amount of force.**_

You can misalign the extruder carriage gantry and your coreXY system will not be square.
{% endhint %}

To check that your system is properly square, align the extruder gantry with the front frame of the Promega as shown in the image below.

The extruder gantry shaft should be parallel to the frame. If one side is off, your system is not square and you will have to readjust tension.

Checking If Your CoreXY is Square

In the image below you can see a coreXY assembly that is not square. The left side is not pulled in as far as the right side. This is because the right side of the gantry is being tugged backwards harder than the left. The solution would be to tension the right side tighter.

A Not Square CoreXY Assembly

## Other CoreXY Tuning Links

{% embed url="https://reprap.org/forum/read.php?397,530210" caption="" %}

## Z-assembly

### Tensioning the Belts

In order to gauge the tension of the Z-axis belts you can pull down on the belt as pictured below.

#### Determining the proper tension on the Z-axis belt is difficult.

{% hint style="warning" %}
More tension gives more accuracy, _**but**_ can cause too much friction for the Z-motor to handle.
{% endhint %}

It is a careful balance and you will become more familiar with the proper tension over time. While pulling on the belt check that the top and bottom clamps are gripping the belt firmly.

#### You should see no evidence of slipping.

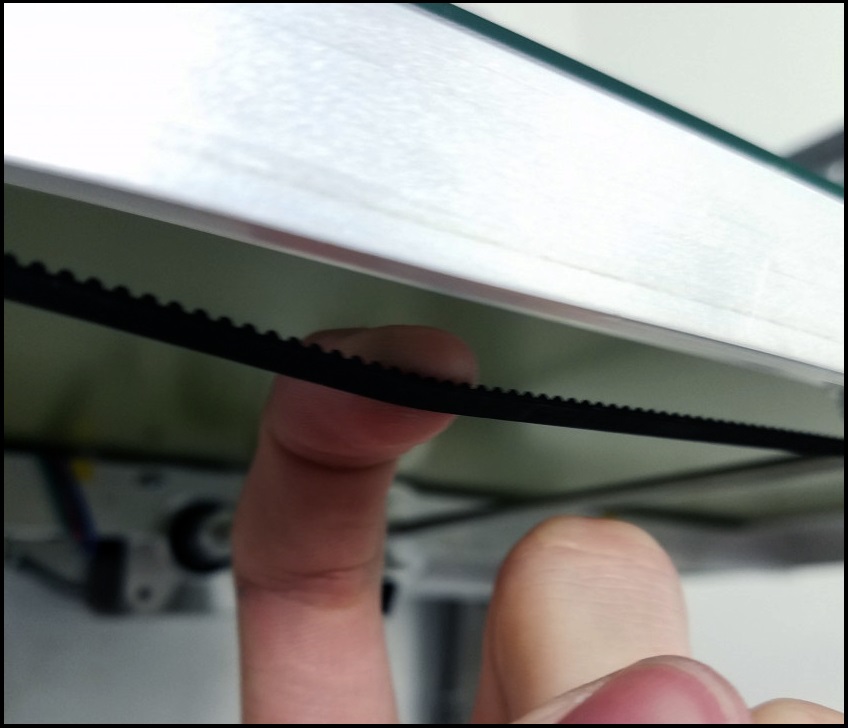
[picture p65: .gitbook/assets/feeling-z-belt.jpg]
Feeling Z Belt Tension


To tension the belt pull up as shown in the picture below, while tightening down the screw underneath the Promega.

{% hint style="info" %}
You should not have to pull hard to achieve the proper tension as tightening down the clamp can tension the belt.
{% endhint %}

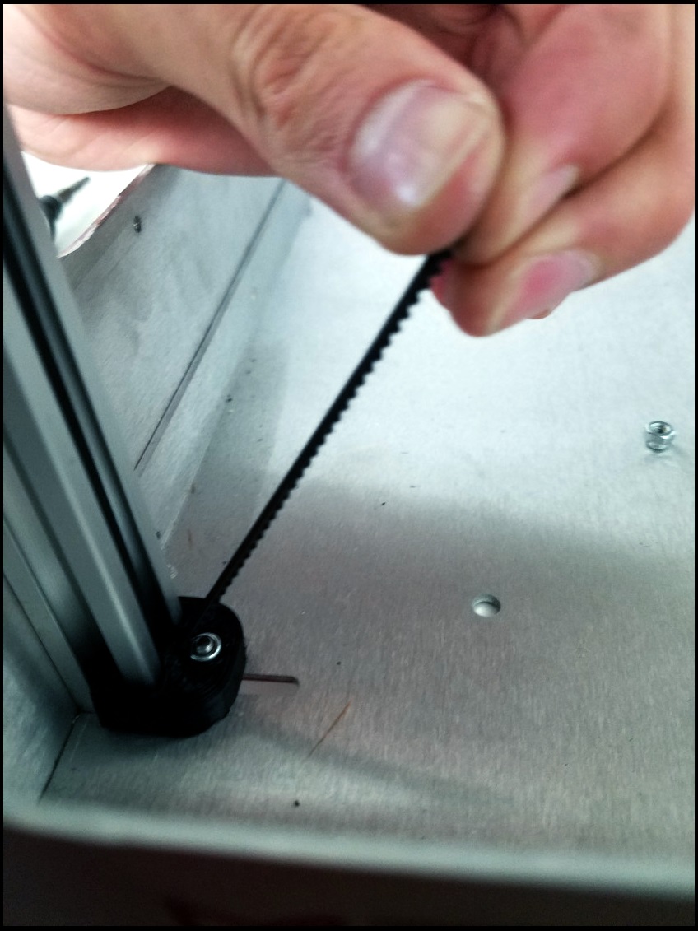
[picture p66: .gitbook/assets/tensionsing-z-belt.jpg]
Tightening Z Belts


Comparing the Distance in Each Corner

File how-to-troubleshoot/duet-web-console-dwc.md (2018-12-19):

# Duet Web Console \(DWC\)

## Rejected by the Duet



### Problem

When attempting to connect to the Promega the error "Your Duet rejected the HTTP request: page not found" is shown. 

This indicates that the web pages of the Duet web server can not be loaded from the SD card. Usually the problem lies in the SD card not being properly mounted to the system. This can happen if you ejected the SD card and then put it back into the Duet board while it was powered. 

### Solution

* Reboot the Duet Maestro board with the microSD card properly fitted inside.
* Reformat the microSD card.
* [Update the microSD card files.]()
* [Update the Duet Web Firmware.](../documentation/software-firmware/updating-firmware.md)

## Frequent Disconnects from the Duet Web Console



### Problem

When working with the Duet Web Console there are frequent disconnects with the Duet Web Console.

### Solutions

* Ensure that your computer has a proper connection to the local network. It is possible that the Duet is not disconnected from the network but your computer is.
* Ensure that the Duet has a proper connection to your local network.
* [Try configuring a static IP address](). It is possible that the router is continuously changing the IP address of your Promega.
* Go to _Settings &gt; General_ on the Duet Web Console and increase the _Status Update Interval_ and _Maximum Number of AJAX Retries_.

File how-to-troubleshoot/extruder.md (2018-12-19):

# Extruder

## Grinding: One Side Keeps Grinding.

### Problem

Only left or right side of my extruder keeps stripping when extruding.

### Solution

#### Wall-E may be tightened, in a skewed position.

Make sure both ports have filament inserted.

Loosen all three M4 screws.

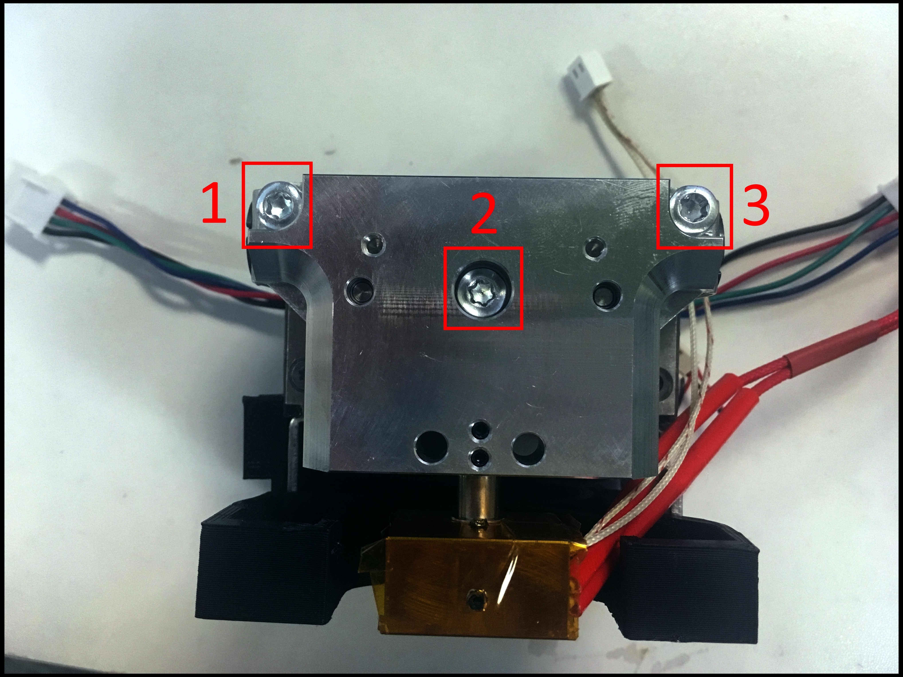
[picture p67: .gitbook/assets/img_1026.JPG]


Look for a shift in the Wall-E position, when loosening. The Wall-E should shift into its natural position, if not already all there.

Lightly tighten the all M4 screws.

Extrude again for 400 mm \(minimum\). Look for a grinding.

If still skipping, continue reading. 

#### There may be artifacts or clogging in your filament path.

Remove the Wall-E. Follow the [Uninstall Extruder](../repair-and-maintenance/install-uninstall/extruder.md#how-to-uninstall) guide.

Remove the plastic insert: [K'Tana](../documentation/mechanical-systems/single-ktana.md#back-components) or [Compound](../documentation/mechanical-systems/compound-mixing.md#back-components).

Look for artifacts.

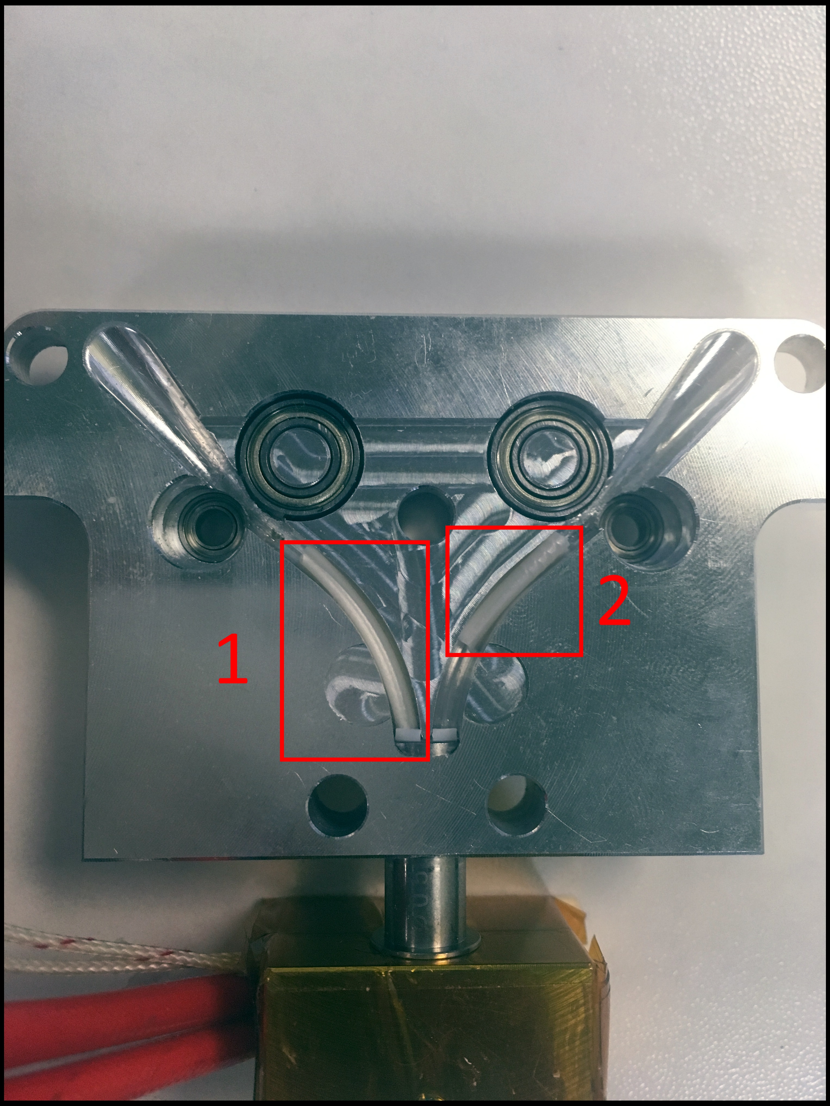
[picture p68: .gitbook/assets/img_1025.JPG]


If it's a clog, follow the [Unclogging Nozzle](../repair-and-maintenance/unclogging-the-nozzle.md) guide.

## Skipping: No Extrusion. All Skipping.

### Problem

I hit extrude. Nothing comes out.

OR

I hit extrude. Only one side extrudes.

### Solution

#### There may be artifacts in your filament path.

Remove the Wall-E. Follow the [Uninstall Extruder](../repair-and-maintenance/install-uninstall/extruder.md#how-to-uninstall) guide.

Remove the plastic insert: [K'Tana](../documentation/mechanical-systems/single-ktana.md#back-components) or [Compound](../documentation/mechanical-systems/compound-mixing.md#back-components).

Look for artifacts.

\#1 is a clog. \#2 is an artifact.

If it's a clog, follow the [Unclogging Nozzle](../repair-and-maintenance/unclogging-the-nozzle.md) guide.

## Skipping: Extrudes, but Skips

### Problem

I am extruding and keep hearing skipping sounds.

### Solution

#### Check your extrusion settings.

Run:

```text
M92; Displays motor steps.
M906; Displays current motor settings.
M350; Displays microstepping settings. 
```

#### Let's check the results with ones below.

_**Compound Mixing**_ Expected Settings:

```text
E Motor Steps: E195.0:191.5:####:####
Motor Current: E400:400:####:####
Microstepping: E128:128:####:####
```

_**Single K'Tana**_ Expected Settings:

```text
E Motor Steps: E198.82:197.00:####:####
Motor Current: E400:400:####:####
Microstepping: E128:128:####:####
```

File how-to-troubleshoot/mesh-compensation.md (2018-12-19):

# Mesh Compensation

## My Bed Is Too Low or High

### Problem 

The nozzle is too high up from the bed. My filament has no chance of sticking to the bed.

OR

The nozzle is scraping against the bed.  Little or no filament is extruding. 

### Temporary Solution

{% hint style="info" %}
This solution only applies during a print. 
{% endhint %}

Open the "Print Status" Tab.

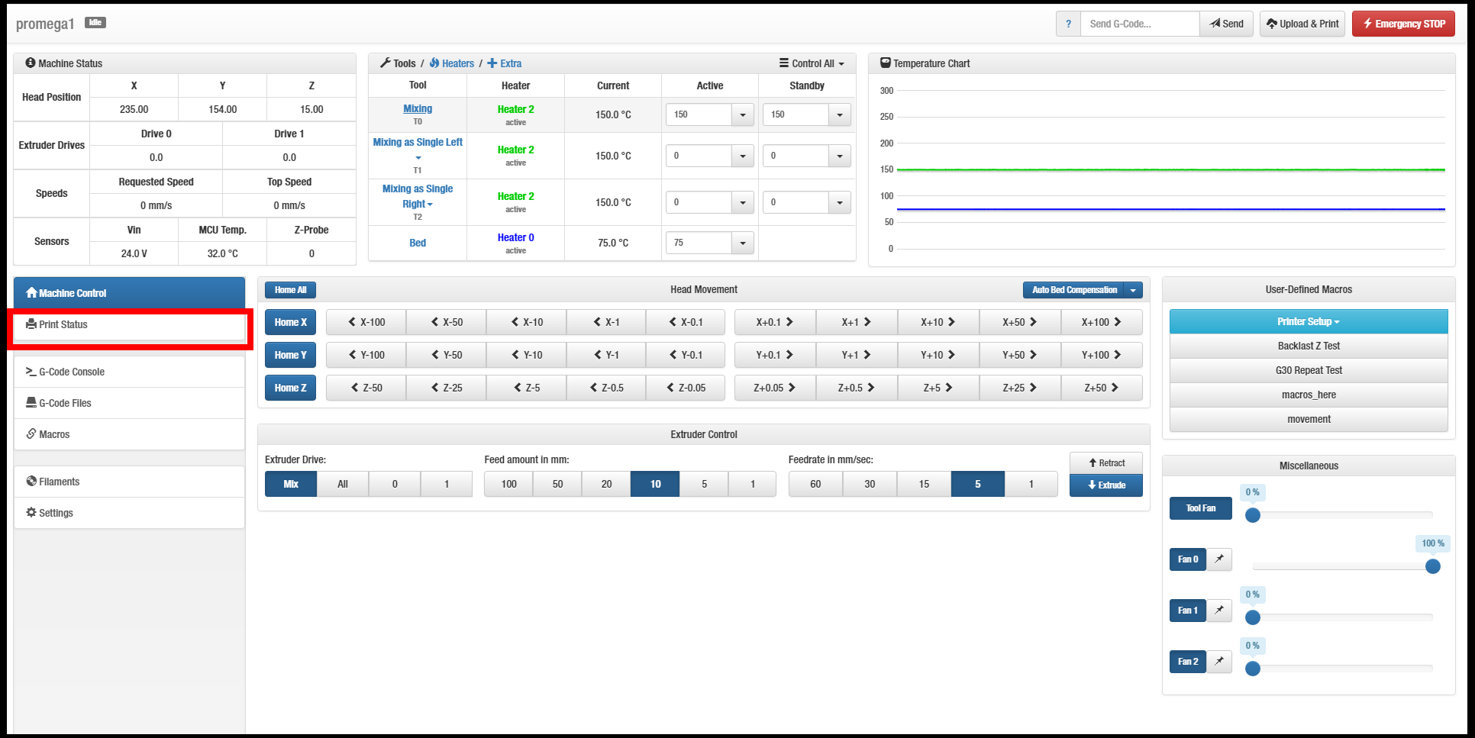
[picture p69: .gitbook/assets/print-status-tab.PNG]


Look for the "Z Baby Stepping" section.

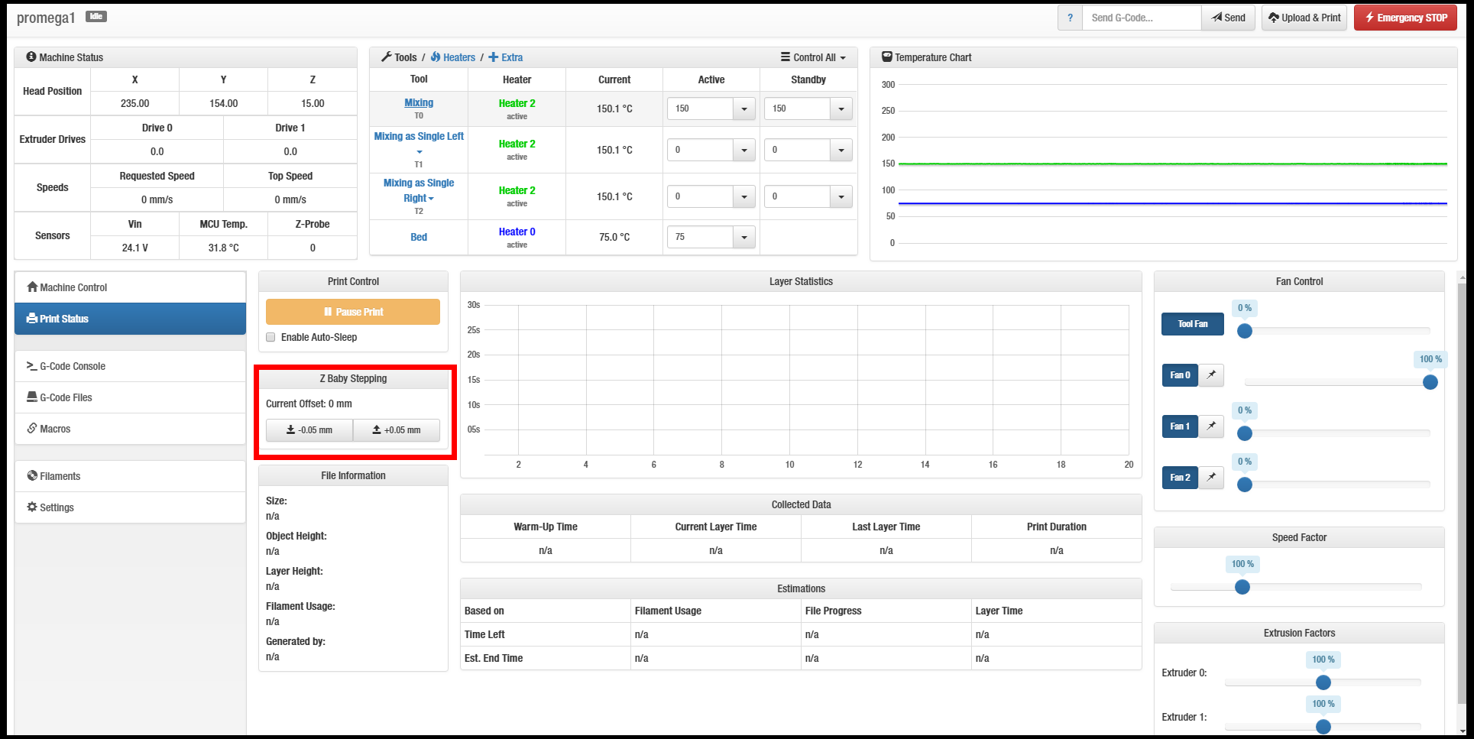
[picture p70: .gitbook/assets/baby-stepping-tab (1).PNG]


Use the two buttons below. 

```text
+ 0.05 mm = Moving the Bed DOWN
- 0.05 mm = Moving the Bed UP
```

{% hint style="info" %}
Use the buttons LIBERALLY. 0.05 mm increments are hard to visually see.

The goal is to manually set nozzle bed height to a desired level. 
{% endhint %}

Mesh grid compensation is NOT disabled. It is shifted, holistically. 

###  Solution

Your Bed Switch's Height Offset parameter not calibrated.

OR

Skipping of bed caused the Height Offset to change.

Follow the [Setup Bed Probe](../beginners-setup-guides/get-your-bed-ready.md) guide.

If you notice any skipping of the bed since the last time mesh compensation probing \(G29\) was preformed, follow the[ Read The Map](../beginners-setup-guides/get-your-bed-ready.md#map-the-bed) guide.

If not, proceed with printing.

{% hint style="warning" %}
Do Not Home The Z after performing a G30. Homing Z _**OVERRIDES**_ any bed level adjustments you just did with the bed probe.   
  
Homing Z serves 2 purposes: 

1\) Allow movements \(No movement can occur without homing first\).

2\) Used for power recovery.
{% endhint %}

## Bed Mesh Compensation Is Not Accurate

### Problem 

Mesh compensation is on and compensating, but the nozzle-bed height is still erratic. 

### Solution

Mesh compensation works within the mesh grid probe.

Check your print's location, with respect to the limits of the mesh grid.

Run:

```text
M557; Mesh Grid Parameters
```

The output should provide the mesh grid limits.

Example:

```text
Grid: X0.0:340.0, Y35.0:380.0, radius -1.0, X spacing 48.0, Y spacing 48.0, 64 points
```

X Minimum: 0

X Maximum: 340

Y Minimum: 50

Y Maximum: 380

## Cannot Find Heightmap.csv

### Problem 

Duet Web Console \(DWC\) throws an error during a print and/or during operation of the printer involving  Heightmap.csv



### Solution

Engage your bed limit switch.

Make sure your bed limit switch is calibrated. If not, follow [Setup Bed Probe](../beginners-setup-guides/get-your-bed-ready.md#setup-bed-probe) guide.

Next, follow the [Map The Bed](../beginners-setup-guides/get-your-bed-ready.md#map-the-bed) guide.

## Bed Mesh Compensation Is Not Activated

### Problem 

The z motor is not actively compensation for bed level variations.

### Solution

Enter code :

```text
M122
```

In the list, look for :

```text
Bed compensation in use:
```

If you see:

```text
Bed compensation in use: none
```

Enter:

```text
G29 S1
```

If you see:

```text
Bed compensation in use: mesh
```

The mesh compensation is activated. Bed compensation typically occur in fine, slow movements. The more angled your bed is, the more active the z-motor is.

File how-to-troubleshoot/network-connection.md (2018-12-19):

# Network Connection

This a complete troubleshooting procedure used to determine the issue behind any connection issues to Duet Web Control \(DWC\).

## DHCP  \(Default Setting\)

### Verify You Have DHCP

Open the "machine\_access.g" file \(located under _sys_ folder\). 

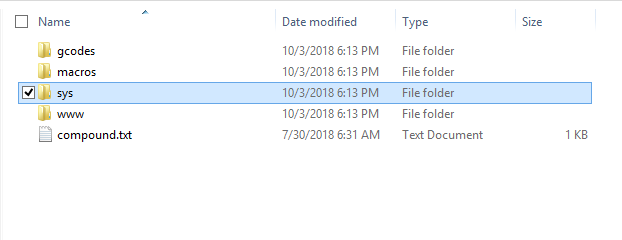
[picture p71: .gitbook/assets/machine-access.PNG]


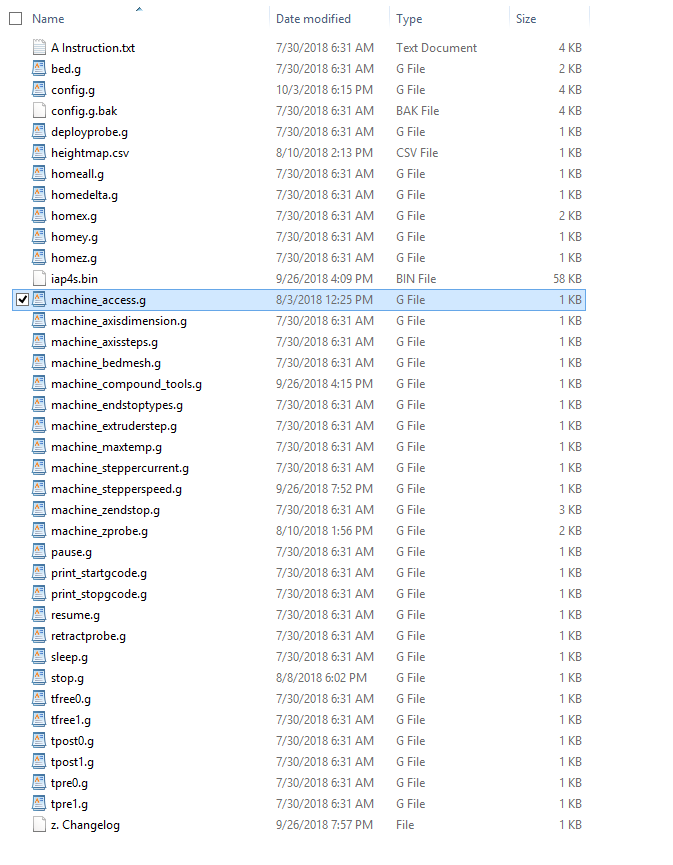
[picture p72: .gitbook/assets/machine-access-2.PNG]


Locate the code: M552

Two things to check:

1. Look for this exact, matching code, with a single line. Dismiss anything after S1.

```text
M552 P0.0.0.0 S1
```

   2. Make sure the semicolon \(**;**\) character is not present before the M552, within the same line.

```text
; M552 P0.0.0.0 S1             ; DHCP - IS - enabled.
M552 P0.0.0.0 S1             ;   DHCP - IS NOT - enabled.
```

If any of these two items are not correct, you may be using a [Static IP](network-connection.md#static-ip).

### Verify IP Substitute Name

Open the "machine\_access.g" file \(located under _sys_ folder\). 

Locate the code: M550.

Your IP substitute name is:

```text
M550 P[here]
```

Example:

```text
M550 PFrankie
```

Enter the name into your web browser: 



Continue if the DWC could not connect:

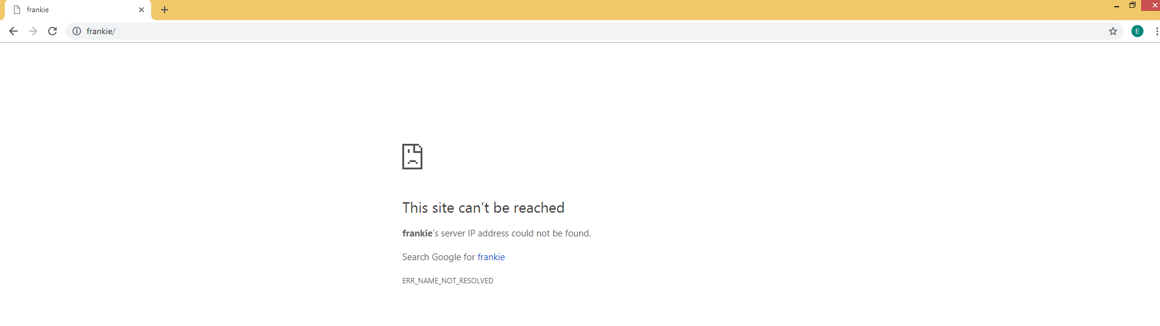
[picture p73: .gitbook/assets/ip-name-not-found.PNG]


### Verify IP Address

#### Follow Duet3D's [Official Getting Connected to Your Duet](https://duet3d.dozuki.com/Guide/1.%29+Getting+Connected+to+your+Duet/7) link.

OR

#### Here is simplified version:

Download [YAT](https://sourceforge.net/projects/y-a-terminal/).

Connect the Duet Maestro \(your board\) to your computer using the USB connection.

Open YAT.

Pick the correct COM\# port. Click "Okay"

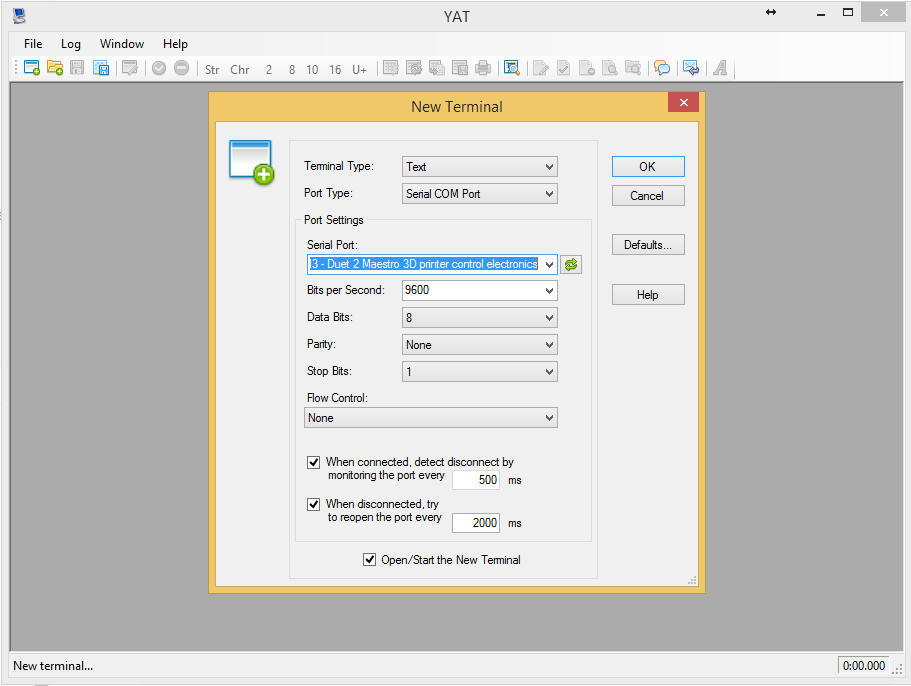
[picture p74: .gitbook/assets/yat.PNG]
If you don&apos;t have the &quot;Duet 2 Maestro 3D printer .. &quot; label show up, it&apos;s not too important.


{% hint style="info" %}
If you want have to "Duet 2 Maestro 3D Printer ..." show up, follow the [Installing the Duet Driver](../documentation/software-firmware/duet-driver.md#how-to-install) guide.
{% endhint %}

Enter code \(into the bar labeled "Send Text"\):

```text
M552
```

Possible Response \#1:

```text
Network is enabled, configured IP address: 0.0.0.0, actual IP address: 192.168.1.##
```

You have a valid IP address. Enter the IP address \(e.g. 192.168.1.54\) into your web browser. 

Possible Response \#2:

```text
Network is disabled, configured IP address: 0.0.0.0, actual IP address: 192.168.1.##
```

Your network settings were disabled \(off\). 

Enter: 

```text
M552 S1
```

Re-evaluate response.

Possible Response \#3:

```text
Network is enabled, configured IP address: 0.0.0.0, actual IP address: 0.0.0.0
```

A 0.0.0.0 IP address means: the Duet \(board\) did not connect to the internet.

Check your internet connection. 

If you're sure the Duet \(board\) has internet connection, move on to the next step.

### Check SD Card 

Make sure the SD Card is installed into your Duet

{pic}

{% hint style="warning" %}
Do Not install or uninstall the SD Card when the printer is on. You May Burn the SD Card by doing this.
{% endhint %}

Return To YAT.

Enter:

```text
M21
```

#### Possible Response \#1 & \#2:

```text
[NOTHING]. Literally nothing.
```

OR

```text
No SD car present.
```

Your SD Card is not being read. 

Make sure the SD Card still works, by verifying you can still see the SD Card's content through your computer.

If you cannot, you need a new SD Card. Refer to [Updating SD Card]() for repopulating your new card.

If you can, we recommend reformatting the SD Card \(follow official Duet3D [microSD guidelines](https://duet3d.dozuki.com/Wiki/SD_Card)\).

**Possible Response \#3 & \#4:**

```text
SD Card mounted in slot 0, capacity ###.##Mb
```

OR

```text
SD Card has open file(s).
```

Your SD Card is being read. Move on to the next step.

### Check SD Card Content

Connect and open the SD Card to your computer.

Make sure your [root folder](https://gopro.com/help/articles/How_To/How-to-Find-the-Root-Level-of-Your-SD-Card) is exactly as shown below:



If not, re-organize until exact.

_OR_

_Delete-all_ and C_opy-Paste_ from [official Promega SD Card Content](https://github.com/PrintM3D/Promega/tree/devel/SD%20Card%20Structure).

Re-install the SD Card into the Duet board. Enter valid IP address or substitute name. 

## Static IP

Under construction. Coming Soon.

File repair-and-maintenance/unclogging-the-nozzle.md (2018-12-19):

# Unclogging The Nozzle

Slide your Cold Section Fan half-way down.

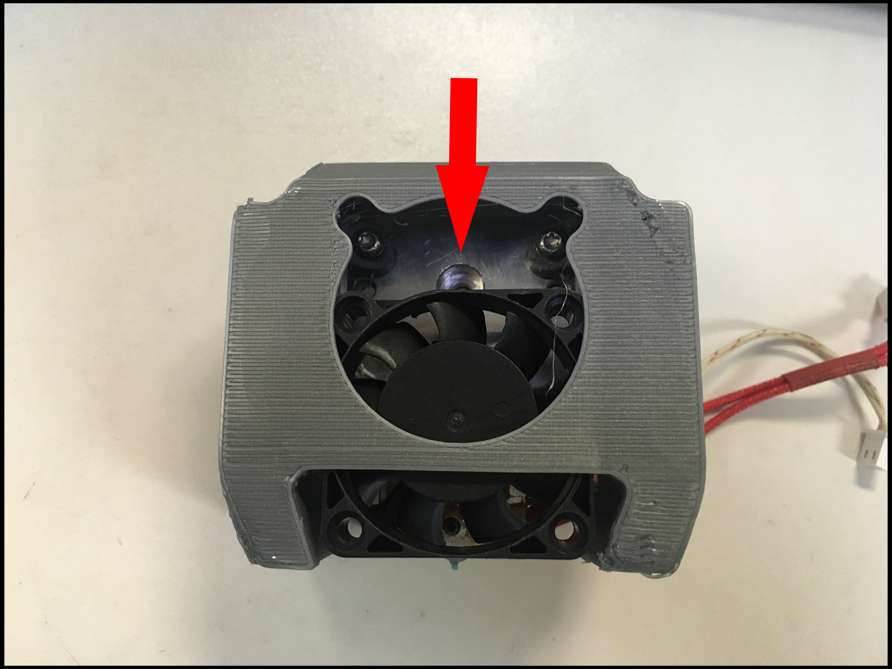
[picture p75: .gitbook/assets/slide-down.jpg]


Unscrew the M3 screws on your Wall-E.



Remove the Wall-E

{% hint style="info" %}
Be cautious. Parts housed in the Wall-E may fall out. Do Not lose them.
{% endhint %}

Carefully bend the filament out of the filament path.

{% hint style="warning" %}
Avoid doing this with PLA or any other brittle filament.
{% endhint %}

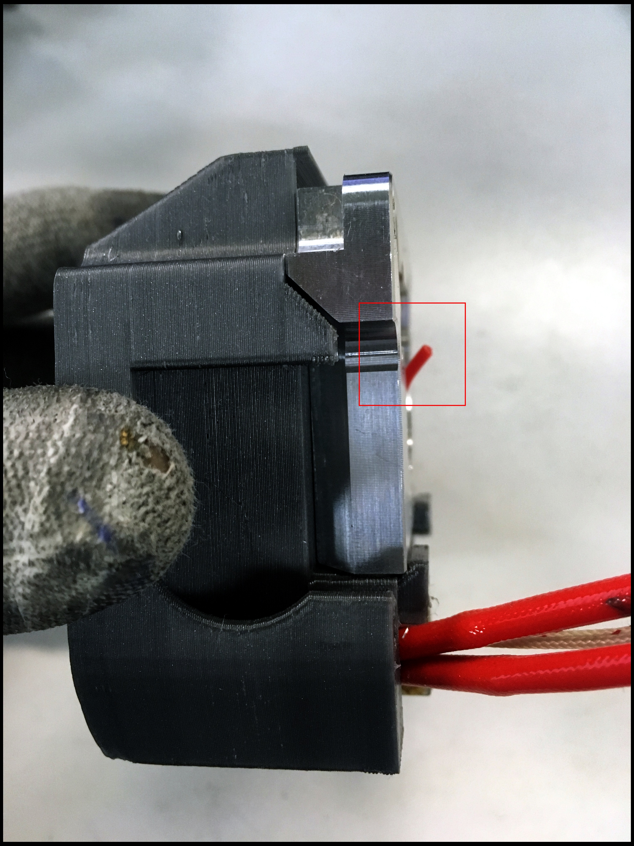
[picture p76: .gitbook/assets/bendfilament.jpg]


Heat the nozzle to 200 C.

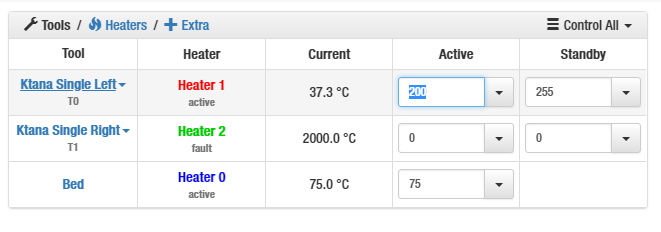
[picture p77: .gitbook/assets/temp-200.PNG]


Wait for the temperature to reach.

Retract the filament out.

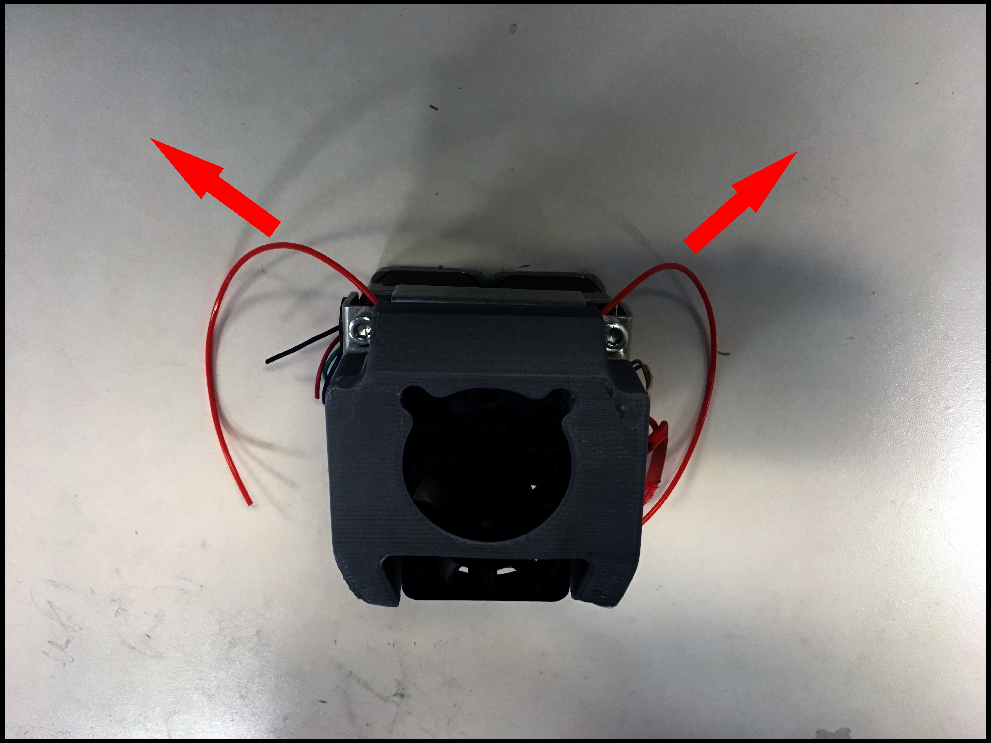
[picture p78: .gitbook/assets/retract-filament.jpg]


Turn off the nozzle

Wait for the nozzle to cool.

Re-install any missing components in the Wall-E.

{% hint style="warning" %}
Double check all components are installed. Failure to do so will prevent the printer from working.  
  
Check using this [Single K'Tana](../documentation/mechanical-systems/single-ktana.md#back-components) or [Compound Mixing](../documentation/mechanical-systems/compound-mixing.md#back-components) parts guide. 
{% endhint %}

Install the Wall-E back into the chassis.

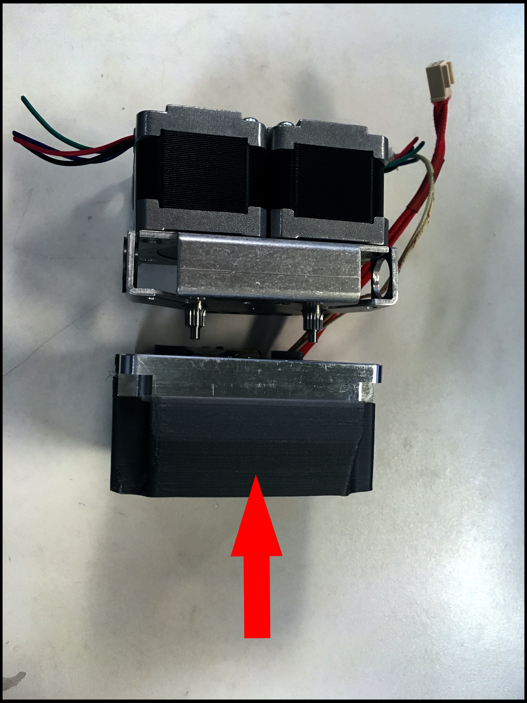
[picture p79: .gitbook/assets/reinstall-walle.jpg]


Use the M3 screws to tighten the Wall-E.

{% hint style="info" %}
Lightly tighten the M3 screws. Do Not Over-tighten.
{% endhint %}

Slide you Cold Section Fan back to original position. 

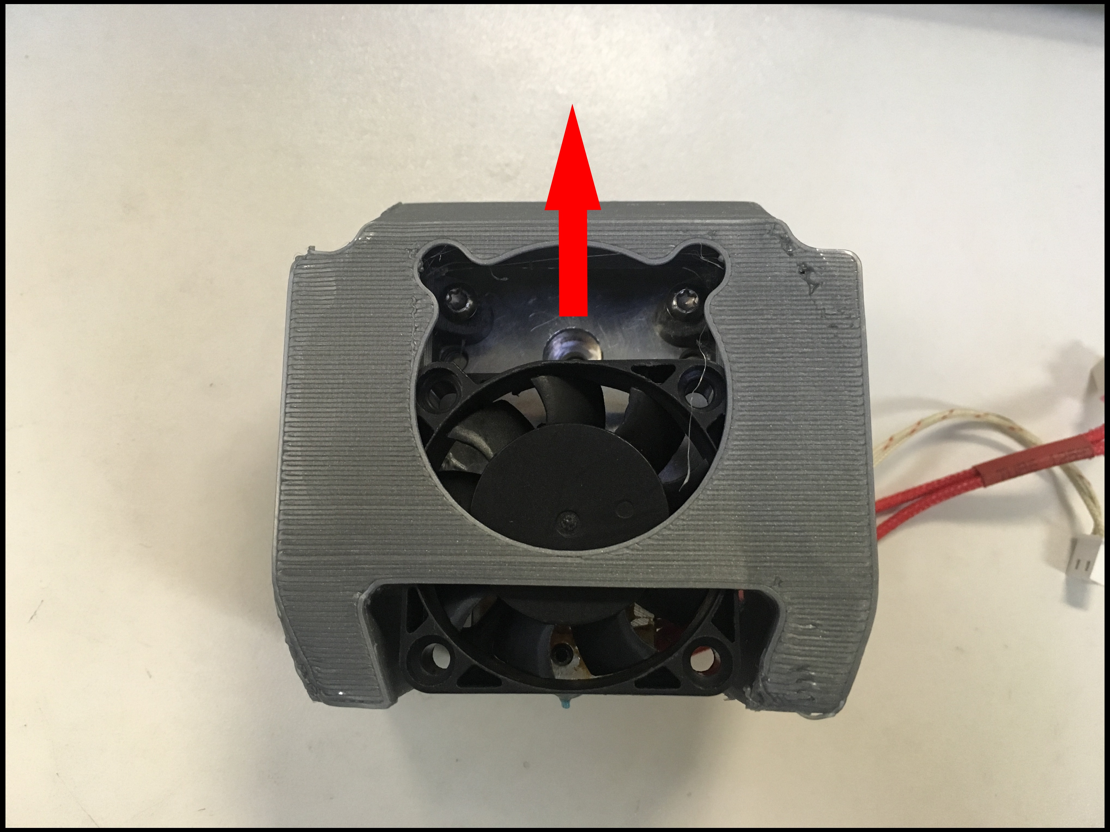
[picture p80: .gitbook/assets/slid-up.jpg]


Done.

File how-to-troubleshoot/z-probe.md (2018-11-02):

# Z Probe

## Z-probe Not Triggering

### Problem

Pressing the Z-probe does not result in a change in Z-probe value in the Duet Web Console _Machine Status_ table.

### Solution

This indicates a broken Z-probe or a problem with the Z-probe wiring. 

#### Z-probe Limit Switch Wiring Problem

The limit switch has an extension cable that extends into the cable chain as it goes to the Duet Board. It is possible that the Z-probe become disconnected from the extension cable during printer use.

#### Let's start.

Turn off the printer.

Open the cable chain segments until you find the connection of the Z-probe limit switch cable to the extension cable.

{% hint style="info" %}
 Read [this guide](../repair-and-maintenance/install-uninstall/cable-chain.md#how-to-open) for more instructions on how to open the cable chain.
{% endhint %}

  

Make sure the cable is properly plugged in. 

{% hint style="info" %}
Polarity does not matter as it is a switch.
{% endhint %}

You can apply glue to the connector to ensure that the connector stays in place. 

Make sure that the cable overall has enough slack for the gantry to move around the entire CoreXY plane.

#### Z-probe IR Probe Wiring Problem

A connection problem has been identified in some of the IR probe connectors. This is easy to fix with the following procedure.

#### Let's start.

Turn off the printer.

Unplug the connector from the IR board.

Take the contact of the white signal cable out of the connector. You will notice that this contact has a U shape on the end. This is meant to properly contact the pin on the IR board, but it does not. Crimp this U so that the tips come closer together.  
  

When inserting the white cable back in the connector it might help to apply a little bit of superglue to keep it in place.

Plug the connector back in the IR board.

Put the fan duct and IR board back in their place.

Test the IR Z-probe.

## Error: Z-probe Triggered Before Move



### Problem

The probing procedure does not start and the Error: Z-probe Triggered Before Move is  printed in the console.

### Explanation

This indicates that the firmware has detected a triggering Z-probe value before it has even started moving the Z-platform. This can be seen in the _Machine Status_ table as the _Z-probe_ value will usually be 1000. The procedure here is attempting to move the Z-platform to the Z-probe in order to trigger it, but the Z-probe is already triggered.

### Solution

Test that the Z-probe value in the Duet Web Console is toggling correctly.

Ensure that the Z-probe is properly connected.

Ensure that the Z-probe is properly configured with the `M558` command.

## Error: Z-probe Not Triggered During Move



### Problem

As the image above indicates, the Error: Z-probe Not Triggered During Move is printed out and the probing operation has failed. If the printer was moving during the probing command, the printer stopped moving before the Z-probe was triggered.

### Explanation

This error is actually a fail safe, the printer is preventing what it presumes is a crash. Since the printer does not know where the mechanical limits of the printer are, it assumes the software limits are the limits of its motion. When the printer is performing its probing procedure it reaches the axes limit before the Z-probe is triggered and prints the error above.  

### Solution

Disable axes limits with the command `M564 S0`

Make sure that the Z-probe value on the Duet Web Console changes when the Z-probe is supposed to be triggered.

Ensure that the printer never reaches a value less than 0 in the Z, during a probe move. You can do this by sending the command `G92 Z50` while the printer is less than 50mm away from the nozzle.

{% hint style="warning" %}
Travelling to a small Z-value after you do this will crash the printer!
{% endhint %}

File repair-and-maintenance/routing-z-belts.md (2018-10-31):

# Routing Z Belts

## Notes

This guide will not cover how to properly tension and level the system. Belt tensioning is covered [here](belt-tensioning.md) and mechanical leveling is covered [here](mechanical-bed-leveling.md).

## Belt Routing

The Z-belts are clamped at the top and bottom by 3D printed clamps. From there, the belt enters a 3D printed block mounted to the Z-platform called the Z-slider.

Z-slider

After the z-slider the belts go to the pulley. If you look on the underside of the Z-platform of the Promega, you will notice that two of the four belts cross over themselves. This allows the bed to be driven by a single motor with a single axle. The belt that crosses over is referred to as the _Flipped Belt_. Follow the section immediately below to route a bed as normal, and the section _Flipped Belts_ to route the flipped belt. When facing the front of the Promega, the right side belts of the Z-platform should have its belts flipped.

Flipped Belts on the Z-assembly

## Normal Belts

Loop the belt through the Z-slider as shown below. The inside of the Z-slider contains bearings that allow the belt to smoothly slide as it is being driven.

Belt-Toothed Idler Mating

After routing the belt through the Z-slider the belt must go around the pulley as shown in the image above.

The belt is then routed back through the Z-slider. The belt should nest comfortably inside the 15x15 aluminum extrusion channel.

The tops and bottoms can now be fastened. Following the [Repairing Broken Belt Clamps](install-uninstall/belt-clamps.md) guide covers installation of the belt clamps. 

To tension the belt system follow [Z-belt Tensioning](belt-tensioning.md#z-assembly) guide.

## Flipped Belts

Loop the belts through the Z-slider. The flat of the belt must be riding the bearing.

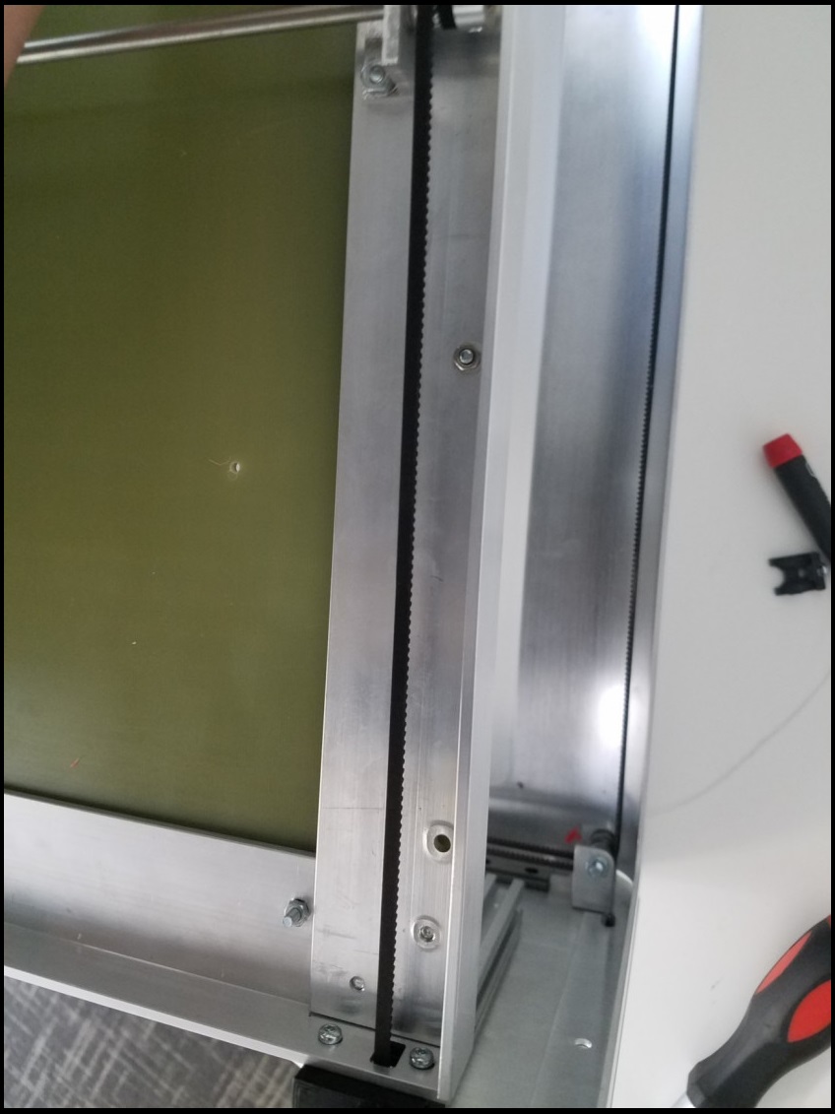
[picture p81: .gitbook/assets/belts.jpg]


Once the belt is through the Z-slider, flip the belt 180 degrees so the teeth can properly mesh with the pulley. Remember to cross the belt as well, if you are routing the belt from the top of the z-slider it should go around the bottom of the pulley.

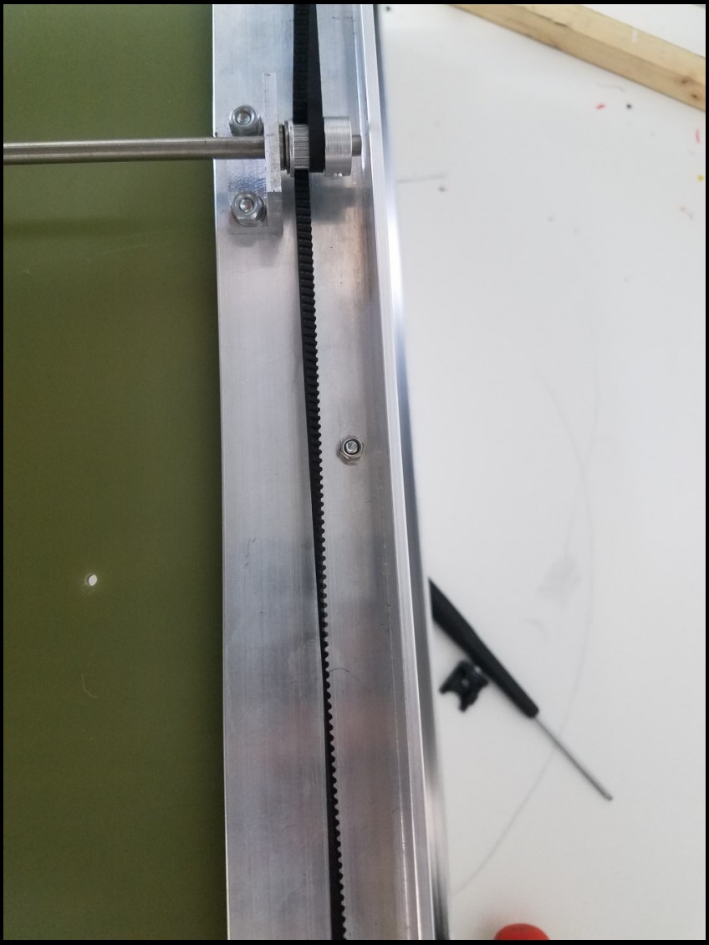
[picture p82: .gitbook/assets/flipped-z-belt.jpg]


When the belt is around the pulley, flip the belt 180 degrees again. **Flip the belt in the right direction!** If you rotate in the wrong direction it will cause the belt teeth to mesh together instead of the flat of the belt. It should look like the image below. **Notice how the two belt flats face each other!**

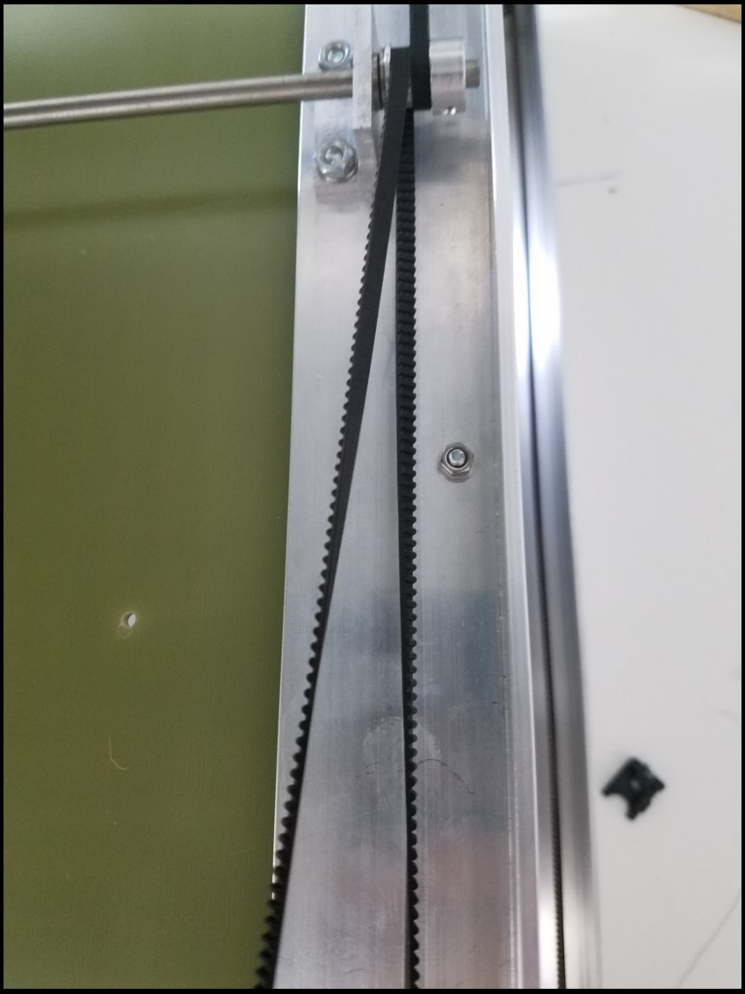
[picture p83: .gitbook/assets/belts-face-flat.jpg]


This is not what the flipped belt should look like, notice how the belts mesh together.

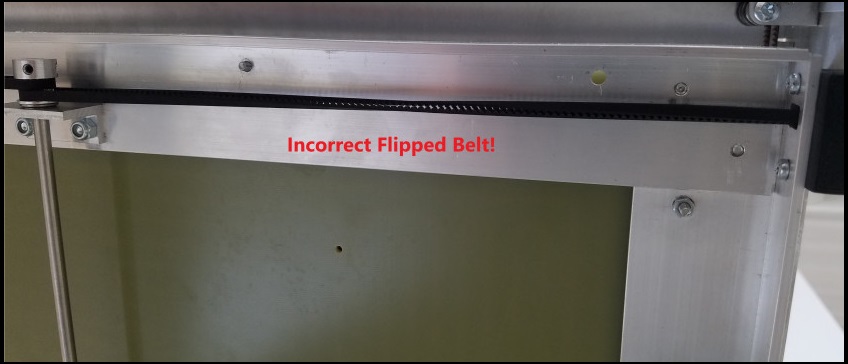
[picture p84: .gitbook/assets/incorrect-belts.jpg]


The final result should look like this:

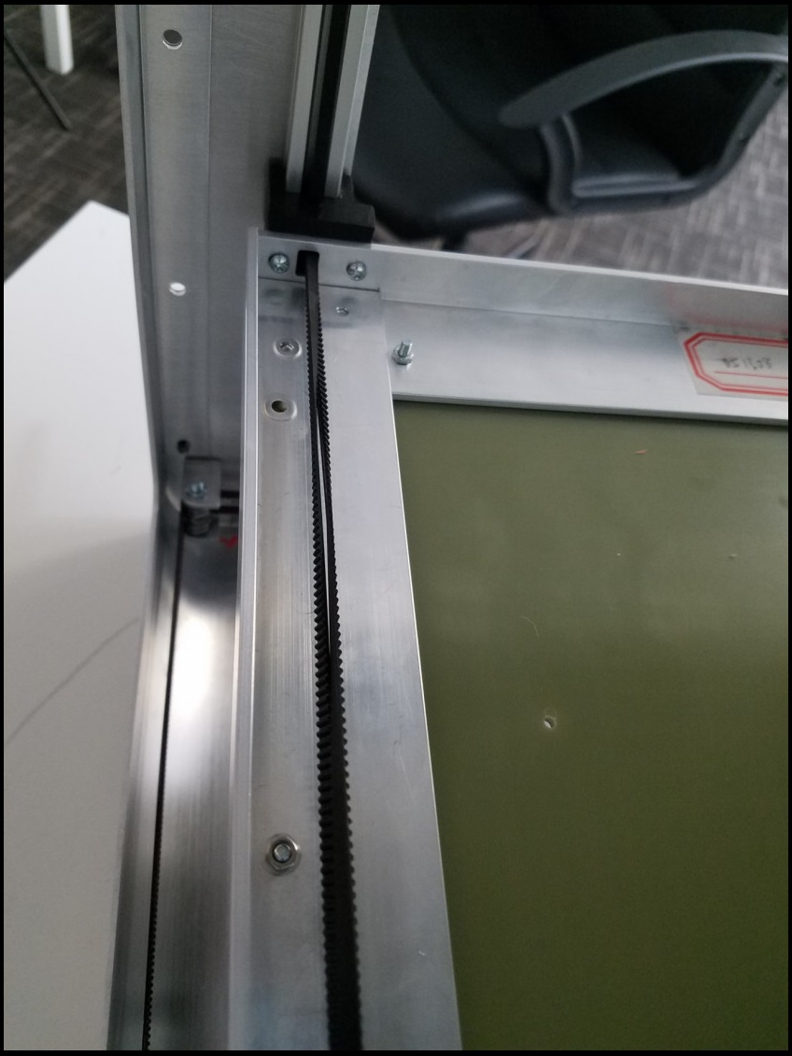
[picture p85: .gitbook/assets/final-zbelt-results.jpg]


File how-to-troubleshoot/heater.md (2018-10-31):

# Heater

## Heater Faults: Temperature Spikes

### Problem

The temperature has an impulse-like increase  - OR - erratic temperature changes. 

### Solution

There is a faulty wire connection. 

Replace PT1000 sensor. 

If replacement does not work, replace PT1000's wire extension. The wire extension is a long wire housed in the [cable chain](../repair-and-maintenance/install-uninstall/cable-chain.md) that extends from the extruder to the Duet board.

## Heater Faults: Temperature Not Rising Fast Enough

### Problem

Heater starts rising in temperature. Then the Duet Web Control \(DWC\) throws a fault, stopping the heating process and/or the print.

### Solution

#### Your Promega may have been placed in a drafty region.

Drafty locations \(e.g. near a ceiling fan\) may cause the heaters \(both bed and/or extruder\) to perform unexpectedly.

We recommend you enclose the Promega.

#### You may need to tune your heater.

Let the heater cool to room temperature.

Make sure you have some space \( estimated: 20 mm\) between the bed and nozzle. We'll will be heating up the heater.

Run:

```text
M562; Removes the fault.
M303 H# S260; Starts heater AUTO-TUNING Heater #. H# is the faulted heater's number.
```

Example: A fault on heater 2.

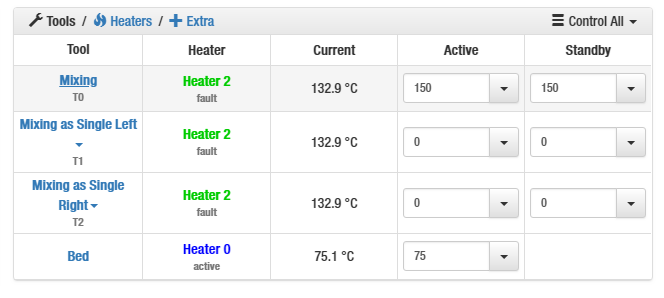
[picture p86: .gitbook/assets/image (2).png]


```text
M562; Removes the fault
M303 H2 S260; Starts heater AUTO-TUNING on Heater 2.
```

Wait for the process to finish. 

{% hint style="warning" %}
Stay with the printer. Do Not Leave the printer unattended while the heater is tuning.
{% endhint %}

Run:

```text
M500; Saves auto-tuning results. Saved in config-override.g (under sys folder)
```

Open: config.g  \(Located in the sys folder, in your SD Card\).

Go to the last line of entire file.

Make a new line. Enter \(if not seen\):

```text
M501; This loads the new auto-tuning results at start up.
```

{% hint style="info" %}
If you see this warning, **Ignore:**

No M501 command was executed in config.g

**Why:** 

You just entered the M501 command into the config.g. The changes to the config.g file will take effect after a restarting your printer.
{% endhint %}

## Heater Faults: Heating Suddenly Stops

### Problem

Everything is working fine. Then a Duet Web Console \(DWC\) suddenly throws this heater fault:

### Solution

Your highest, allowable heater temperature was passed.

Run:

```text
M143 H#; H# is faulted heater's number
```

The default maximum heater temperature is 320 C.

## Heater Faults: Temperature is 2000C!

### Problem

My temperature reads continuously reads 2000 Celsius.

### Solution

The PT1000 is completely disconnected.

Check your PT1000 cables are connected. Use the [Duet Maestro Wiring Diagram](https://duet3d.dozuki.com/Wiki/Duet_2_Maestro_Wiring_Diagram) to figure out which cable is that. If connected, continue.

Replace the PT1000.

## Bed Fault: Not Heating Up

### Problem

Your bed is not heating up uniformly or not heating up at all. 

### Solution

**Turn OFF the printer FIRST**

Check if your bed power switch is on. 

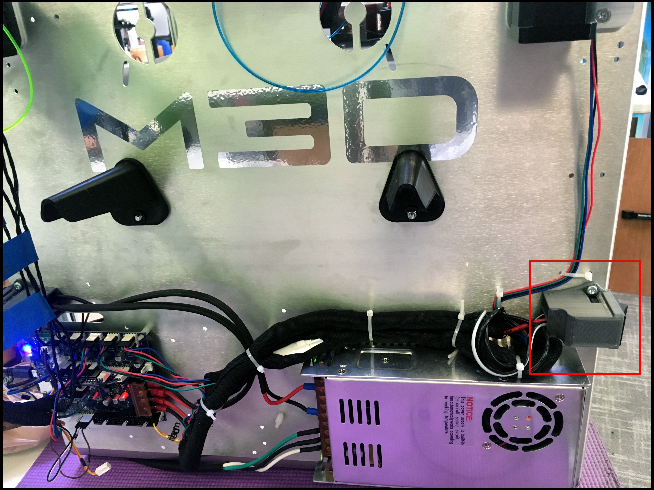
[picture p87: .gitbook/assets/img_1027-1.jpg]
Location of the Bed Power Switch


Check the screw terminals that connect the bed to the Duet. Check these terminals on both the Duet side and the heated bed side. It is possible that they loosened up and are not making proper connection. 





Feel the wires going into the terminals and move them around to see if they are loose. If they are open the terminal cover and screw them down tight again with a Phillips head screwdriver.

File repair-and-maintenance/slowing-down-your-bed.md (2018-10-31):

# Slowing Down Your Bed

If you bed crashes against the nozzle or another part of the extruder it will cause the Z-axis motor to skip. The motor skips to prevent damage to a glass bed or the Z-platform itself. This skip can also cause your bed to misalign, if this occurs, follow the [Mechanical Leveling](mechanical-bed-leveling.md) guide to fix this issue.

Once the Z-motor skips it will power off and will not hold the position of the bed. Due to the weight of the bed and the lack of friction the bed can fall with speed. This can be dangerous, therefore it is best to **keep clear of the Promega while it is moving.** The speed of the fall of the bed can be reduced greatly by:

* Properly tensioning the Z-assembly belts according to the [Belt Tensioning](belt-tensioning.md#corexy-tuning) guide.

In addition, tighten the Z-motor belt by loosening the two screws on the bottom of the Z-platform and pulling the motor as shown in the image below.

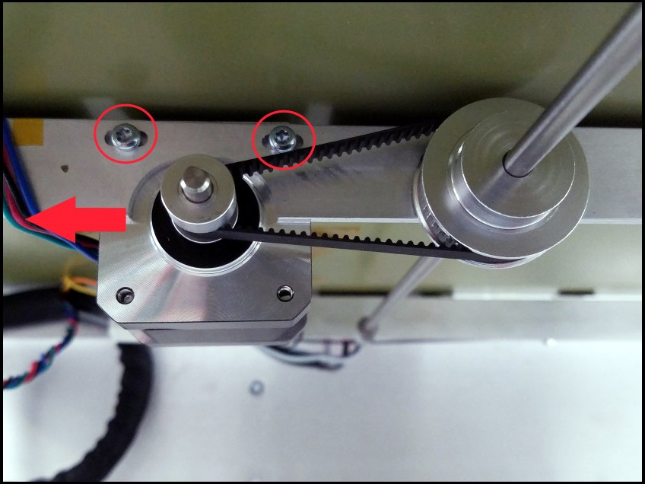
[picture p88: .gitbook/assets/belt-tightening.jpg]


Tighten the Z-motor belt pulley against the rail in order to increase friction.

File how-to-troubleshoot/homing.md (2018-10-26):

# Homing

## Won't Complete: Just Keeps Skipping

### Problem

I starting homing. The printer starts moving and then it just keeps skipping. It never homes.

### Solution

#### **Your limit switch may not work.**

Let's see if your limit switches works.

Run:

```text
M18 X Y; This disables the CoreXY (motion) motors
```

Slowly move the extruder head to the center

Run: 

```text
M564 H0; Let's you move the motors without homing.
G91;
```

Manually engage \(press down\) on the X, Y, and Z Limit Switch. We recommend using tape.

{% hint style="warning" %}
We discourage using your fingers. Do so at your own risk. 
{% endhint %}

Run:

```text
G1 Y100 S1;
G1 X100 S1;
G1 Z100 S1;
```

#### Let's evaluate:

If the _**extruder moves forward or backward,**_ 

* The Y Limit Switch is not working.

If the _**extruder moves to either side**_, 

* The X Limit Switch is not working.

If the _**bed moves down**_,

* The Z Limit Switch is not working. 

## Homing Z: Weird Z Endstop Values

### Problem

I am calibrating my z endstop value. After I home Z, the Z endstop value is not what I put.

### Solution

#### Your new z endstop value may not be saved.

Let's check what your current Z Endstop Value is.

Go to _**Settings**_. Then click the _**System Editor**_ tab. Open the _**machine\_zendstop.g**_ file. 

Scroll down to the last line.

Check your Z Endstop Value. Is this the calibrated value?

{% tabs %}
{% tab title="YES" %}
Change it to a new value.

Click "Save Changes" button.

Home the Z.

Check to see if your Z Endstop Value is correct.

If not, continue reading.
{% endtab %}

{% tab title="NO" %}
Continue reading. 
{% endtab %}
{% endtabs %}

#### Your machine boundaries may be too low.

Let's check if your machine boundaries are interfering. 

Go to _**Settings**_. Then click the _**System Editor**_ tab. Open the _**machine\_axisdimension.g**_ file. 

Look for the line labeled " Maximum"

```text
M203 X# Y# Z#; Maximum
```

Is this value smaller than your new Z Endstop Value?

{% tabs %}
{% tab title="YES" %}
This value MUST be at least 0.5 mm above your calibrated Z Endstop Value.

Add 0.5 mm to your new Z Endstop Value. This is your new Maximum Z Value.

Change the Z value to the new Maximum Z Value.

Click "Save Changes"

Home the Z.

Check to see if your Z Endstop Value is correct.

If not, continue reading.
{% endtab %}

{% tab title="NO" %}
Continue reading. 
{% endtab %}
{% endtabs %}

#### Your mesh compensation may be changing the value.

Home the Z.

Run:

```text
G29 S2
```

The Z Endstop Value should now be the calibrated value.

Mesh compensation is changing the value of your Z Endstop Value. 

Proceed with printer operation.

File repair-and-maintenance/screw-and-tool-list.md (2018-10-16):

# Screw & Tool List

## Notes

Look under the All Tools header for each assembly to see all the possible tools you will need to maintain, assemble or repair the Promega .

Look under the [All Screws](screw-and-tool-list.md#all-screws) section to view a more in-depth list of the screw types and their location.

## Brief Overview

### All Tools

* T20 Torx Screwdriver
* T10 Torx Screwdriver
* T6 Torx Screwdriver
* 1.5mm Hex Driver
* 1.3mm Hex Driver
* 5 mm Nut Driver 
  * \(or Pliers/Adjustable Wrench\)
* 5.5 mm Nut Driver 
  * \(or Pliers/Adjustable Wrench
* 7 mm Nut Driver
  * \(or Pliers/Adjustable Wrench\)
* Needle-nose pliers

### All Screws

* Hot-end Block: 1.3 mm Hex
* Hot-end Extruder Set screws: 1.5mm Hex
* Fan duct & Z-Probe: T6 Torx
* Other screws: T10 or T20 Torx

## Detailed List

### Extruder Assembly

#### Tools

* 1.3 mm Hex
* 1.5 mm Hex
* T6 Torx Screw Driver
* T10 Torx Screw Driver
* T20 Torx Screw Driver

#### Screws

**1.3 mm Hex**:

* PT1000 Setscrew
* Heater Cartridge Setscrew
* Nozzle Setscrew

**1.5mm Hex**:

* Hot-end Setscrews

**T6 Torx**:

* Fan Duct Bolts \(2x\)
* Z-Probe Limit Switch Mount \(2x\)

**T10 Torx**:

* Cable chain bolt
* Cold-section fan \(2x\)
* Extruder Wiring Assembly \(2x\)

**T20 Torx**:

* Extruder block mount \(3x\)
* Belt clamp \(2x\)

### CoreXY Assembly

#### Tools

* T10 Torx Screwdriver
* T20 Torx Screwdriver
* 1/4-20 Hex

#### Screws

**T10 Torx**:

* CoreXY Stepper Motor \(6x\)
* Belt Routing \(8x\)
* Linear Slider Mounts \(6x\)
* X & Y Limit Switch Mounts \(4x\)

**T20 Torx**:

* CoreXY Gantry Brackets \(2x\)
* Belt Routing \(4x\)
* Motor mount \(6x\)

**1/4-20 Hex**:

* CoreXY Rods \(4x\)

### Z-Assembly

#### Tools

* T10 Torx Screwdriver
* T20 Torx Screwdriver

#### Screws

**T10 Torx**:

* Bottom belt clamp \(4x\)
* Linear Slider Mount \(12x\)
* Heated Bed / PCB Mount \(12x\)
* Z-Slider Screws \(8x\)
* Limit Switch Mounts Screws \(2x\)
* Z-motor Screws \(2x\)

**T20 Torx**:

* Linear Bottom Screws \(4x\)
* Bed Frame Screws \(12x\)

### Wiring Assembly

#### Tools

* T10 Torx Screwdriver
* T20 Torx Screwdriver

#### Screws

**T10 Torx**:

* Duet Board \(4x\)

**T20 Torx**:

* Power supply \(4x\)
* Bed switch \(2x\)
* Power switch \(2x\)
* Filament holder

**Phillips Head**:

* Bed Terminals
* Power Supply Terminals
* Duet Board Terminals

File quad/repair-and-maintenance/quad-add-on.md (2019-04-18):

---
description: Under Construction
---

# Install

## What is the Quad Add-On?

## Tools

* T10 Screwdriver
* T20 Screwdriver
* Small Flat-Head Screwdriver
* Philips-Head Screwdriver
* Medium-size Pliers
* Adjustable Wrench 
  * Recommended: M6 Hexagonal Driver Bit \(for bolts\)

{% hint style="info" %}
Details, on when to use them, as shown throughout the install guide.
{% endhint %}

## Additional Hardware

* Super Glue

{% hint style="info" %}
Details, on when to use them, as shown throughout the install guide.
{% endhint %}

## How To Install

#### Turn off Power

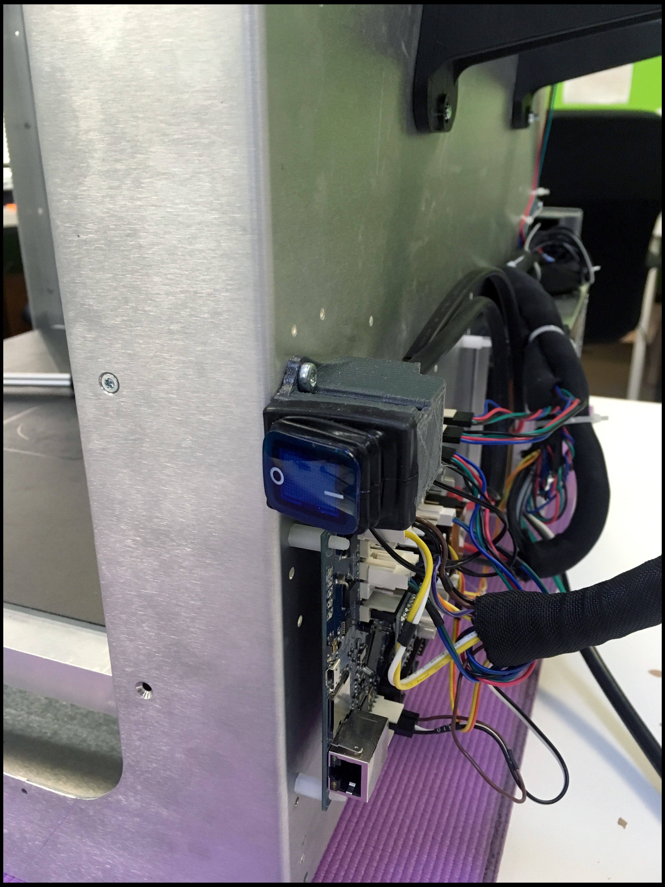
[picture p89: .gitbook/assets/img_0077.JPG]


#### Unplug Power Supply

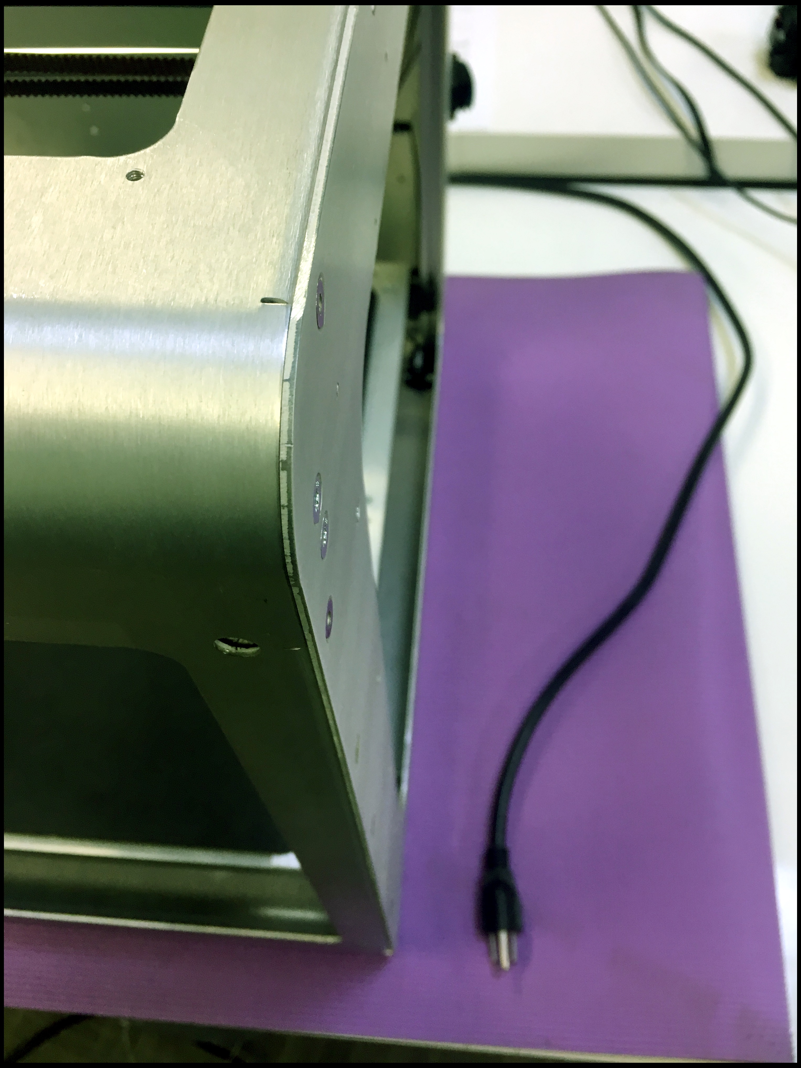
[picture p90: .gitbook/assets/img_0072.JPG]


#### Remove Wall-E

{% embed url="https://youtu.be/ESNClgTFywQ" caption="" %}

{% hint style="success" %}
Tools:

* Small Flat-head Screwdriver
* T10 Screwdriver
* T20 Screwdriver
{% endhint %}

#### Remove Cable Chain

{% embed url="https://youtu.be/Q8EUlI4kuD4" caption="" %}

{% hint style="success" %}
Tools:

* Philips Head Screwdriver
{% endhint %}

\*\*\*\*

#### **Unfasten Gantry Belt Clamp**

{% embed url="https://youtu.be/VqGK6qcCMn8" caption="" %}

{% hint style="success" %}
Tools:

* T20 Screwdriver
{% endhint %}

#### Remove X Axis System

{% embed url="https://youtu.be/bmPePS8jyVc" caption="" %}

{% hint style="success" %}
Tools:

* T10 Screwdriver
{% endhint %}

#### Remove Extruder

{% embed url="https://youtu.be/HNqaTdfDCok" caption="" %}

{% hint style="success" %}
Tools:

* Adjustable Wrench 
  * Recommended M6 Hexagonal Driver Bit \(for bolts\)
{% endhint %}

#### Prep Promega-Quad Adapter

{% embed url="https://youtu.be/HQ3qw7pvMn0" caption="" %}

{% hint style="success" %}
Tools:

* Pliers
* T10 Screwdriver

Additional Hardware:

* Super Glue
* 2x Small Cylindrical Magnets \(Provided\)
* 2x M3 Locknuts \(Provided\)
{% endhint %}

#### Install Promega-Quad Adapter

{% embed url="https://youtu.be/rw6SntHdPPg" caption="" %}

{% hint style="info" %}
Take the time to make sure your Promega-Quad Adapter slides smoothly.
{% endhint %}

{% hint style="success" %}
Tools:

* Adjustable Wrench
  * Recommended: M6 Hexagonal Driver Bit \(for bolts\)
{% endhint %}

#### Prep Cable Chain

{% embed url="https://youtu.be/Iu5SqmuvGWc" caption="" %}

{% hint style="success" %}
Tools:

* Small Flathead Screwdriver

Additional Hardware:

* Quad \(Long\) Motor Cables \(Provided\)
{% endhint %}

#### Prep Duet Maestro

{% embed url="https://youtu.be/rAeKsvmrjq4" caption="" %}

{% hint style="info" %}
Double check your electronics
{% endhint %}

{% hint style="success" %}
Tools:

* Electronics Gloves \(recommended\)

Additional Hardware:

* Motor Expansion Board \(Provided\)
{% endhint %}

#### Install X Axis System

{% embed url="https://youtu.be/zAK7kCCi-Oc" caption="" %}

{% hint style="success" %}
Tools:

* T10 Screwdriver
{% endhint %}

{% hint style="info" %}
The holes used to fasten the X Axis System shown below:
{% endhint %}

Left Gantry Slider \(symmetric for the right side\)

#### Loosen Motors

{% embed url="https://youtu.be/1OxzPaosM7E" caption="" %}

{% hint style="success" %}
Tools:

* T10 Screwdriver
* T20 Screwdriver
{% endhint %}

#### Install Belts

{% embed url="https://youtu.be/FVCRk-dd-tg" caption="" %}

{% hint style="info" %}
Use a small Flat-head screwdriver to help with routing the belts through the idlers.
{% endhint %}

{% hint style="success" %}
Tools:

* Small Flathead Screwdriver
{% endhint %}

#### Tighten Belts

{% embed url="https://youtu.be/2EsqSvQU-Bg" caption="" %}

{% hint style="info" %}
Double check your X Axis System is straight.
{% endhint %}

{% hint style="success" %}
Tools:

* _**NONE**_
{% endhint %}

#### Tighten Motors

{% embed url="https://youtu.be/ndXeUfurlK8" caption="" %}

{% hint style="info" %}
Double check your X Axis System is straight.
{% endhint %}

{% hint style="success" %}
Tools:

* T10 Screwdriver
* T20 Screwdriver
{% endhint %}

#### Install Quad

{% embed url="https://youtu.be/gxBcfXwyrY0" caption="" %}

{% hint style="info" %}
Use the small Flat-head screwdriver to move the M3 nuts to the correct position.
{% endhint %}

{% hint style="success" %}
Tools:

* T10 Screwdriver
* Small Flat-head Screwdriver
{% endhint %}

#### Install Cable Chain

{% embed url="https://youtu.be/SGv8X08vIUo" caption="" %}

{% hint style="success" %}
Tools:

* T10 Screwdriver
{% endhint %}

#### Connect Quad

{% embed url="https://youtu.be/o\_meHtOtH3g" caption="" %}

{% hint style="success" %}
Tools:

* T10 Screwdriver
* Small Flat-head Screwdriver
{% endhint %}

#### Adjust Bed Limit Switch

{% embed url="https://youtu.be/fZXRubA6xzU" caption="" %}

{% hint style="success" %}
Tools:

* Small Flat-head Screwdriver
{% endhint %}

#### Check Wire Slack

{% embed url="https://youtu.be/NyKIuQjD4FA" caption="" %}

{% hint style="success" %}
Tools:

* Small Flat-head Screwdriver
{% endhint %}

#### Plug-in Power Supply

## Additional Electrical Changes

### Jumpers need to be re-positioned.

Before:

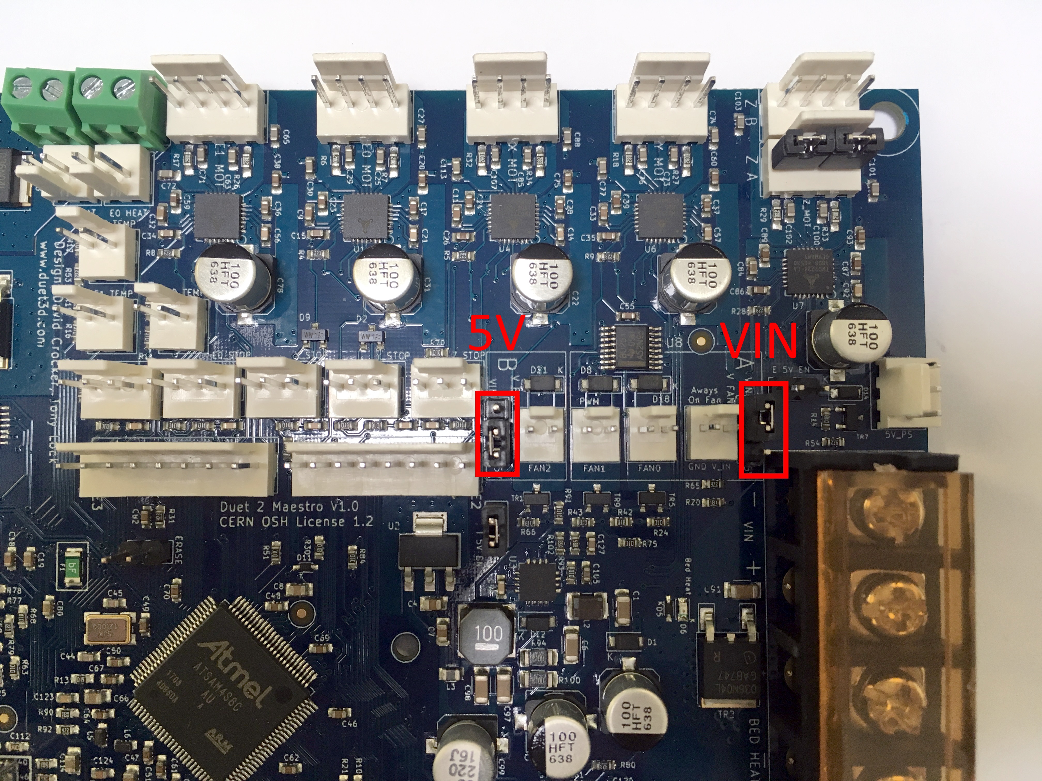
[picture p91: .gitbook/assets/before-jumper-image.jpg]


After:

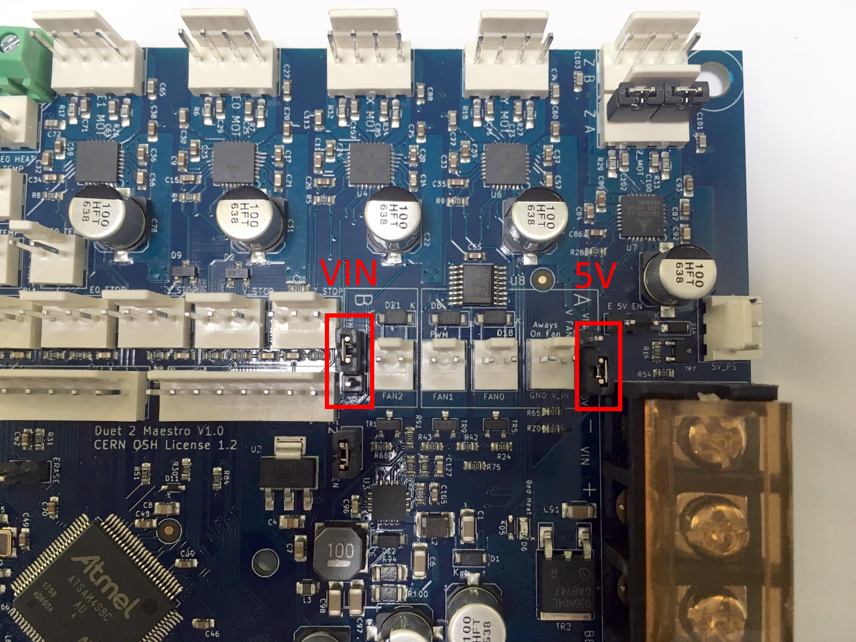
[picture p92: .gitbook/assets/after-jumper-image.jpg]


### Fans need to be reconfigured.

Two Methods:

Change Fan Connections **\(Recommended\)**

{% embed url="https://youtu.be/x\_1gCOkPz-A" %}

\*\*\*\*

Swap Crimps \(Advanced\)

{% hint style="danger" %}
### Proceed at own risk. Similar changes are done in-house by trained personnel for assembled Promega-Quads.

Make sure Promega is OFF during reconfiguration.
{% endhint %}

{% embed url="https://youtu.be/YA3u8R11ZE4" caption="" %}

### Plug In Motor Cables

Location of Motor Cable Connections on Board:

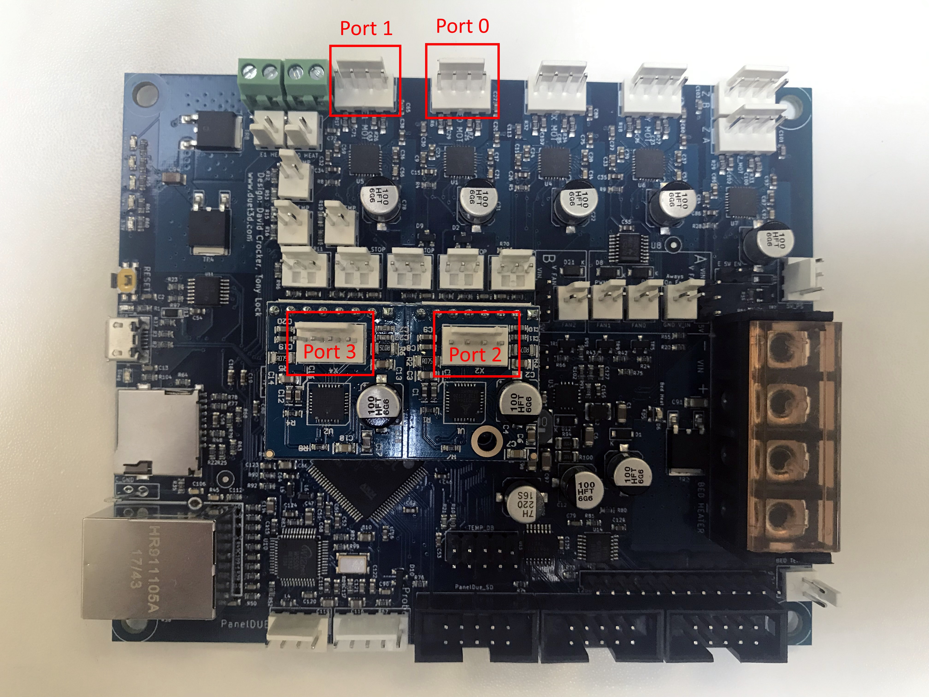
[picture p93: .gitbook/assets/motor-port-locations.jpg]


When plugging in motor cables, match the dots:

Left-side: Port 1, Right-side: Port 0

Left-side: Port 3, Right-side: Port 2

{% hint style="warning" %}
CAREFULLY & FULLY plug in the motor cables into their designated spots. 

The pictures above are partially plugged in \(for sake of seeing the markings\). 
{% endhint %}

## Additional Software Changes

Go to [GitHub](https://github.com/PrintM3D/Promega)

Download the Promega Source File.



Delete ALL content in SD Card.

Go to .../Downloads/promega-devel/Promega-devel/SD Card Structure/Quad.

Copy ALL and paste into SD Card.



Ready For Printing.

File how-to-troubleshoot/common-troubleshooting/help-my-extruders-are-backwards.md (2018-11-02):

# Help! My Extruders Are Backwards

Whenever you are changing or updating configuration files it is possible that your heaters or extruders will be wrongly configured. This could result in your extruder drivers going the wrong way, or the left extruder spinning when you want the right extruder to spin.

## Flipping Extruder Directions

This will fix extruder drives that are going backwards. For example if you pressed the button _Extrude_ on the Duet Web Console it will result in the drive pushing filament back out of the extruder hole as if you were retracting. **Heads-up read the information box below.** If you implement this fix, and in the future update to new configuration files, it will undo these changes.

{% hint style="info" %}
It is possible that your extruder directions are flipped because the extruder drives are flipped, meaning left is wired to right and right is wired to left. Check that your left extruder \(drive 0\) does actually move the left extruder and that the right extruder \(drive 1\) actually moves the right extruder.
{% endhint %}

Connect to the Promega's Duet Web Console

To check your extruder directions go to the _Machine Control_ tab in the Duet Web Console and select drive 0 or 1 in _Extruder Control._ Then try to feed filament into the extruder and see if your directions are correct. It is also possible to change the extruder drives in the section below. If your filament is being pushed out of the top of the extruder when you press extrude, follow the steps below.  
  

Go to the _Settings_ tab of the Duet Web Console and then to the _System Editor._  
  

Open the _config.g_ file. Find the block with the following commands:  
`; --- SECTION: DRIVES (MOVEMENT SECTION) & ENDSTOPS ---`

`M667 S1 ; Enable coreXY mode   
M569 P0 S0 ; Drive 0 goes forwards, CoreXY_1   
M569 P1 S1 ; Drive 1 goes forwards, CoreXY_2   
M569 P2 S1 ; Drive 2 goes forwards, Z Motor   
M569 P3 S0 ; Drive 3 goes forwards, Left Extruder   
M569 P4 S1 ; Drive 4 goes forwards, Right Extruder`

Change the `P3` and `P4` drive directions with the `S` parameter. For example, if my left extruder was going backwards, I would change the command to go from `M569 P3 S0`

 to`M569 P3 S1.`

Save the file and reboot the system. Repeat step 2 to confirm that the directions are correct.

## Flipping Extruder Drives

This section will fix extruder drives that are flipped. If you actuate what you think is the right drive and it results in the left drive spinning and vice versa. **The inherent problem here lies in wiring, so be aware, the fix you are applying is temporary.** The wiring is intended to have the left extruder wired to extruder drive 0 and the right extruder to extruder drive 1. If you implement this fix, and in the future update to new configuration files, it will undo these changes. To fix this permanently fix the wiring of your Promega in the [Extruder Wiring](../../documentation/electronics/extruder-assembly-wiring.md) guide. The fix below is fine to implement, but will provide a temporary solution.

Connect to the Promega's Duet Web Console

To check your extruder drives go to the _Machine Control_ tab in the Duet Web Console and select drive 0 or 1 in _Extruder Control._ If you have extruder drive 0 selected and press extrude it should move the left extruder. For extruder drive 1, the right extruder should move.  It is also possible to change the extruder drives in the section below.    
 

Go to the _Settings_ tab of the Duet Web Console and then to the _System Editor._  
  

Open the _machine\_compound\_tools.g_ \(or _machine\_ktana\_tools.g_\) __file. And find the `M563`  commands, this configures the tool:  
`M563 P0 D0:1 H2 F2 S"Mixing" ; Define mixing tool` 

`M563 P1 D0 H2 F2 S"Mixing as Single Left" ; mixing nozzle only using left extruder motor  
M563 P2 D1 H2 F2 S"Mixing as Single Right" ; mixing nozzle only using right extruder motor`

For the tools with only one drive \(the `D` parameter\) you will have to change the drive. If it was using `D1` change it to `D0` and vice versa. You are telling the firmware to use drive for 0 or 1 for specific tools.

Save the file and reboot your printer.

Check the direction of the drives now as you might have to now flip the directions of the extruder drives.

## Changing Tool Heaters

Just like in the section above, you can use the `M563` command in order to change which tool uses which heater. This section will fix a heater that is wired to the wrong port of the Promega, or configured wrong. This will present itself in the form of a heater fault, or a thermistor error value of 2000°C.The Promega configuration expects heater 1 to be assigned to the left tools and left extruder, and heater 2 to be assigned to the right tools and right extruder. Remember that heater 0 is the heated bed in the configuration files. 

Connect to the Promega's Duet Web Console    

Go to the _Settings_ tab of the Duet Web Console and then to the _System Editor._  
  

Open the _machine\_compound\_tools.g_ \(or _machine\_ktana\_tools.g_\) __file. And find the `M563`  commands, this configures the tool:  
`M563 P0 D0:1 H2 F2 S"Mixing" ; Define mixing tool` 

`M563 P1 D0 H2 F2 S"Mixing as Single Left" ; mixing nozzle only using left extruder motor  
M563 P2 D1 H2 F2 S"Mixing as Single Right" ; mixing nozzle only using right extruder motor`

Change the heater number \(`H` parameter\) assigned to the tools above. It should be either `H1` or `H2` .

Save the file and reboot the Duet.

Look for a change in temperature reading on the Duet Web Console. If it is displaying a proper value, you can try to heat up the heater.

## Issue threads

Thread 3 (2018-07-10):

Replace old links

daniel-farina, 2018-07-10:
@flipthedog
There are some links that need to be updated before we make the official switch tomorrow.  Use [this search ](https://github.com/PrintM3D/Promega-Docs/search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)

flipthedog, 2018-07-10:
**Fixed!**

Closed 2018-07-10.

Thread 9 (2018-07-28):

Z-Level doc mentions IR probe, but no instructions on how to use

zorrobyte, 2018-07-28:
https://github.com/PrintM3D/Promega-Docs/blob/master/getting-started/z-probe-calibration-and-bed-leveling.md

The docs say, "The Promega comes equipped with two different Z-probes, the limit switch and the IR probe. This guide can be followed to configure either one." -- https://promega.printm3d.com/getting-started/z-probe-calibration-and-bed-leveling But doesn't have instructions on how to actually switch to the IR probe.

Why are there two probes? Is one more effective than the other?

TheBum, 2018-07-28:
The IR probe was the original plan, but it doesn’t work well when using a glass sheet. The limit switch was added more or less at the last minute to address that.

zorrobyte, 2018-07-28:
My printer came with a buildtak sheet, like many others. Maybe it’ll be
worth documenting anyway. I’ll try to write something up soon if I can find
the Duet docs explaining it.

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

zorrobyte, 2018-07-28:
Which sensor does the Promega use?
https://duet3d.dozuki.com/Wiki/Connecting_a_Z_probe

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

Closed 2018-08-03.

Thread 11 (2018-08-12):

Extruder change documentation is out of date

leonmf, 2018-08-12:
- The extruder change documentation shows an older style wiring harness system.
- The instructions tell the user to remove the hot end and hold it in place while unplugging cables that can't be reached.
- The diagrams should show exactly which connectors to use for which items with labeled red circles.

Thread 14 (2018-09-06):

Better describe changes?

DMCShep, 2018-09-06:
**Problem Areas**

[https://promega.printm3d.com/changelog](https://promega.printm3d.com/changelog)
Also
[https://github.com/PrintM3D/Promega-Docs/commits/master](https://github.com/PrintM3D/Promega-Docs/commits/master)

**Current Behavior**

GitHub commit log is filled with change descriptions such as "one page and 10 assets modified", "one page modified", "25 pages and 13 assets modified", "Update changing-sliders.md", which requires careful review of each commit to gather intent of why the change was made. It is not immediately clear what changed or why with as many as 25 pages involved.

The promega.printm3d.com changelog has an abundance of "Updated Printed Parts" changes, without any reason for why changes were required or made. This leads to guys with earlier printers like myself not knowing what parts would be of serious benefit and what can be outright ignored. (It does seem some revisions are meant for ease of assembly while others are meant for better printer operation -- obviously only one of those two matters once the printer arrives intact.)

Additionally, the printed parts themselves do not have any visual on the GitBook page, so a "guess and check" approach is required to know if the right part has been downloaded _at all,_ let alone if it matches what you already have or not. Especially for parts where it is important to have the latest revision, this can make it harder to tell what's good and what's not.

**Expected Behavior**
1. GitHub commit log adequately describes changes
2. promega.printm3d.com changelog states why changes were needed and made
3. Thumbnails for all STL files for clarity of both A) _what_ the part is, and B) what _changed_ between iterations.
4. Minimum suggested STL revision for each printed part, in case being behind a revision or two is still okay

This would clear a lot of confusion up about the changes going on in the GitBooks. Thank you! 👍

sohjsolwin, 2018-09-06:
Linking to: [Promega Issue](https://github.com/PrintM3D/Promega/issues/8)

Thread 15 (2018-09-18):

Guide for replacing Z-Sliders

sohjsolwin, 2018-09-18:
There is currently a guide for replacing Z-Clamps, but nothing for Z-sliders. Considering this is a part that more than a few early Promega users have received cracked, it would be beneficial to have a guide for how to replace them.

sohjsolwin, 2018-09-18:
Relates to [Promega Issue #23](https://github.com/PrintM3D/Promega/issues/23)

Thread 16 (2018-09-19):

Pic Zoom

DMCShep, 2018-09-19:
**Problem Area**
https://promega.printm3d.com/ (global)

**Current Behavior**
High-res images are provided on the website, however there is no easy way to view them in full resolution without downloading them entirely. This can make viewing fine details harder than it should be.

**Desired Behavior**
Some kind of feature where you click on the image and it zooms (Lightbox.js, etc.) would be wonderful, especially if you can click left/right arrows to see the close-ups.

sohjsolwin, 2018-10-02:
I may be a limitation of the system they're using that can't be changed. In case it is, I would recommend using a browser extention, such as Imagus, which will open an image in a larger floating window at full resolution whenever you hold your mouse over it.
Example:
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

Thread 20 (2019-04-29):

Guide missing what part needs ot be regularly lubricated/maintained

c-schmitz, 2019-04-29:
There is currently no indication on the wiki where, what and how to lubricate moving parts.
There is no recommendation on what lube is to be used.
The printer is delivered with minimal lubing (if at all) and soon fails because of that.
You need a section in the wiki for that.

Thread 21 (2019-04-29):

No information on filament guidance with mounted glass panels

c-schmitz, 2019-04-29:
It is currently completely unclear how the filament is supposed to be guided to the compound head if the glass panels are installed.

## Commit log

2018-07-23 Automatic Bed Leveling Compensation fixes
    Added Step 5 to perform a G30 probe before starting on the bed mesh. Changed the G29 to G32 so that bed.g is invoked.
2018-08-05 Update temperature-calibration.md
    Updated temp doc to more clearly showcase the auto-tune steps.
2018-08-06 GitBook: [master] 29 pages and 72 assets modified
    [051108_c1-rear-cable-harness_base.STL, 051108_d1-rear-cable-harness_base.STL, 051112_b1-spool-holder.STL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]
2018-08-06 GitBook: [master] 4 pages and one asset modified
    [051296_b4-z-slider_rv14_1.STL]
2018-08-07 GitBook: [master] one page and one asset modified
    [051296_b4-z-slider_rv14_1 (1).STL]
2018-08-26 Update bed-leveling-and-probing.md
    IR probe steps where not spaced and hard to read. added spacing and proper numbering
2018-09-01 GitBook: [master] 6 pages and one asset modified
    [058052_a3-nozzle-fan-guide.STL]
2018-09-11 GitBook: [master] 3 pages and 2 assets modified
    [058052_a4-nozzle-fan-guide.STL, a2-external-filter-fan.STL]
2018-10-02 Update an intro to tools with high temp info
    added a small section about high temp nozzles to the tools and temperature section.
2018-12-19 Update unboxing-and-assembly.md
    repopulating with previous content, due to folder name change.
2019-02-18 Update check-your-printer.md
    Copying all material in mechanical-check.md to this new page.
2019-03-13 Added image and STLs of Y Limit Housing XL
    For longer motors
    [y-limit-housing-xl-v2_1.stl, y-limit-housing-xl-v2_2.stl]
2019-03-13 Added image and STL links for Y Limit Housing XL
    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
